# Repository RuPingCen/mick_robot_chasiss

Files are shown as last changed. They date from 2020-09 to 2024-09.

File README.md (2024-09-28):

# mick_robot_chasiss

项目文档：https://mickrobot.github.io/ 

本项目描述了针对室外环境设计的一个开源ROS小车底盘，项目开源了小车的3D机械图，基于STM32设计的小车控制板，电源板（为传感器供电）；小车的**PCB**、**代码**及**3D图纸**均是开源，大家可以自行下载打样学习。

- **master分支 为第3版小车 MickX4-V3（ 最新版）**，
- MickX4-V2分支为第2版小车代码分支。 
- M4分支为麦克纳姆轮第一版小车代码分支。[项目更新日志](https://github.com/RuPingCen/mick_robot_chasiss/tree/master/更新日志.md)

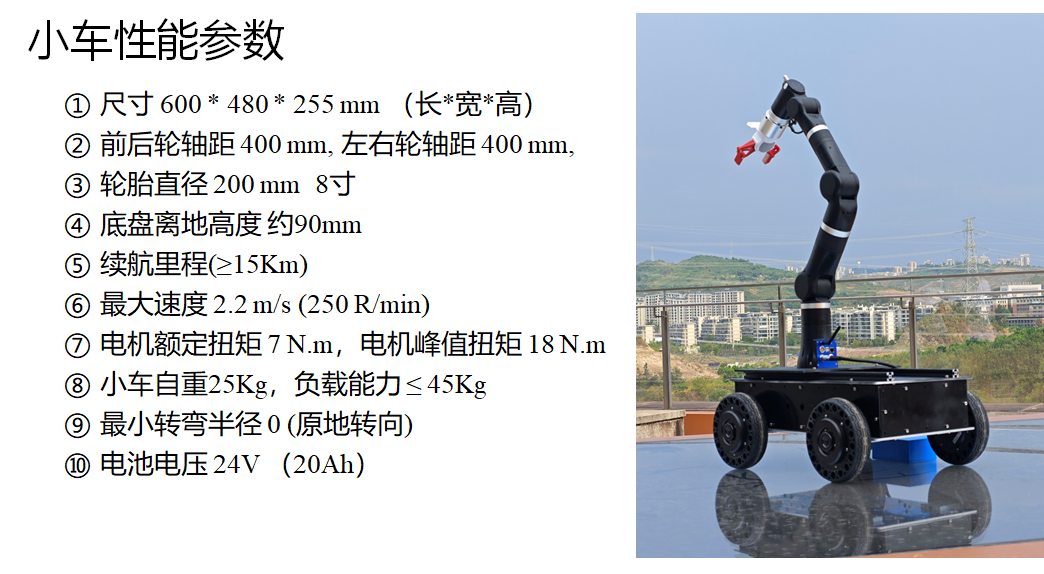
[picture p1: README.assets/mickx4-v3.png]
mickx4-v3-1




**文件目录说明**

- **ROS_Node**：小车底盘配套的ROS节点，其功能为对外发布小车里程计数据，接收ros cmd_vel话题控制命令控制小车移动

- **STM32_Code**：存放小车上嵌入式控制板的代码文件，控制器采用STM32F407

- **3D_Model_xxx**：存放小车3D模型文件

- **PCB_File**：存放小车上所用PCB文件

- **Reference_Documents**：存放相关的传感器的使用手册等

------------------------------------------------------------------------------------------

注意：开源的电源板和控制板仅供大家自己打样学习用，切勿用于商业用途。问题、项目合作可联系 cenruping@vip.qq.com，可以代为调试、新开发线控底盘或针对已有的小车底盘设计**工业版控制器**及**大功率电源模块**。也欢迎加QQ群讨论交流  1149897304 (开源ROS自主导航小车)；

- 小功率电源板-[淘宝链接](https://item.taobao.com/item.htm?spm=2013.1.w4023-18698948782.10.3cd752e6AWcwLT&id=702856225631)
- 大功率电源模块-[淘宝链接](https://item.taobao.com/item.htm?spm=a213gs.success.result.1.5ac34831gMQFX4&id=746778756080)
- 控制板-V1-[淘宝链接](https://item.taobao.com/item.htm?spm=2013.1.w4023-18698948782.7.5ec21803wgmf68&id=649231129557)

------------------------------------------------------------------------------------------

## 1 启动差速小车底盘
master分支代码文件可适配**两轮**、**四轮差速小车**。两轮差速底盘，需要把底盘电机ID设置为1和3即可使用4轮差速底盘相同的命令。

###  1.1 连线配置小车

==注：==[小车的搭建、连线，遥控器操作说明](https://github.com/RuPingCen/mick_robot_chasiss/tree/master/小车组装说明.md) 

### 1.2 启动小车ROS节点

ROS节点与控制板的通讯协议：  https://docs.qq.com/sheet/DV2hmSEdSYVVtclB4 

小车的配套的ROS节点位于 https://github.com/RuPingCen/mick_robot_chasiss/tree/master/ROS_Node 

该**ROS_Node**目录中包含两个文件夹： **mick_bringup**和**mick_description** ，**mick_bringup**为小车对应的ROS驱动节点，**mick_description**为urdf模型。

**step1:** 将ROS_Node中的mick_bringup目标代码拷贝到ROS工作空间进行编译

```shell
cp -r mick_bringup ~/catkin_ws/src
cd ~/catkin_ws/src
catkin_make
```

**step2**： 通过USB转232串口线连接电脑和小车控制板，

修改串口权限（可以查看设备的ID号 ls /dev/ttyUSB*）

```
sudo chmod 766 /dev/ttyUSB0
```

 或者根据串口设备的标识符去设置串口别名

```
cd mick_bringup/scripts
sudo cp ultrasonic.rules /etc/udev/rules.d/
```

把文件拷贝到/etc/udev/rules.d目录下就可以使用 /dev/mick替代 /dev/ttyUSB0 来访问模块了

**step3:** 启动ROS节点

```shell
roslaunch mick_bringup mickrobot_v3.launch
```

小车节点启动以后可以通过rostopic list命令查看到该ROS节点会对外发布如下Topic

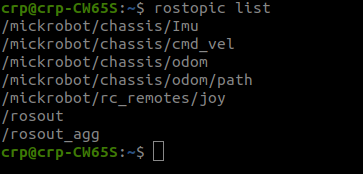
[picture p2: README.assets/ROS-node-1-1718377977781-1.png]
ROS-node-1


其中：

- /mickrobot/chassis/Imu     对外发布小车自身IMU测量数据
- /mickrobot/chassis/odom  小车里程计数据
- /mickrobot/chassis/odom/path   小车里程计数据对应的路径（默认不发布）
- /mickrobot/rc_remotes/joy  遥控器数据（默认不发布）
- /mickrobot/chassis/cmd_vel    小车控制命令接收话题

mickrobot_v3 launch文件内容如下：

```xml
<launch>
  <node pkg="mick_bringup" type="mickx4_bringup_v3" name="mickrobot" output="screen">

	  <param name="dev" value="/dev/ttyUSB0" type="str" />
	  <param name="baud" value="115200" type="int" />
	  <param name="time_out" value="1000" type="int" />
	  <param name="hz" value="100" type="int" />

	  <param name="chassis_type" value="0" type="int" /> <!--0: 差速底盘  1: 麦克纳姆轮底盘 2:阿卡曼转向  3全向-->

	  <param name="sub_cmdvel_topic" value="chassis/cmd_vel" type="str" />
	  <param name="pub_odom_topic" value="chassis/odom" type="str" />
	  <param name="pub_imu_topic" value="chassis/Imu" type="str" />
	  
	  <param name="is_pub_path" value="1" type="int" /> <!--0: 不发布底盘轨迹  1: 发布 -->
	</node>
</launch>
```

**step4**: 新建终端，通过ROS话题向  **/mickrobot/chassis/cmd_vel** 话题发布数据 控制小车移动（**注意 将遥控器左上角拨码开关拨到最上，表示开启自动驾驶模式**）

```shell
rostopic pub /mickrobot/chassis/cmd_vel -r 10 geometry_msgs/Twist "linear:
  x: 0.0
  y: 0.0
  z: 0.0
angular:
  x: 0.0
  y: 0.0
  z: -0.1" 
```

角速度方向： 逆时针为正，速度方向：车头方向为x方向。

**step5**:  或通过键盘遥控小车底盘（step4和step5选其中一个即可）

这里借助turtlebot3提供的键盘控制节点，检验小车与ROS节点通讯是否正常

注意：需要安装  **sudo apt-get install ros-noetic-turtlebot3-teleop** 包

```shell
export TURTLEBOT3_MODEL=burger
roslaunch turtlebot3_bringup turtlebot3_model.launch
```

## 2 小车控制板

## 2.1 小车控制板V3

第3版小车控制板采用了STM32F407作为主控制器

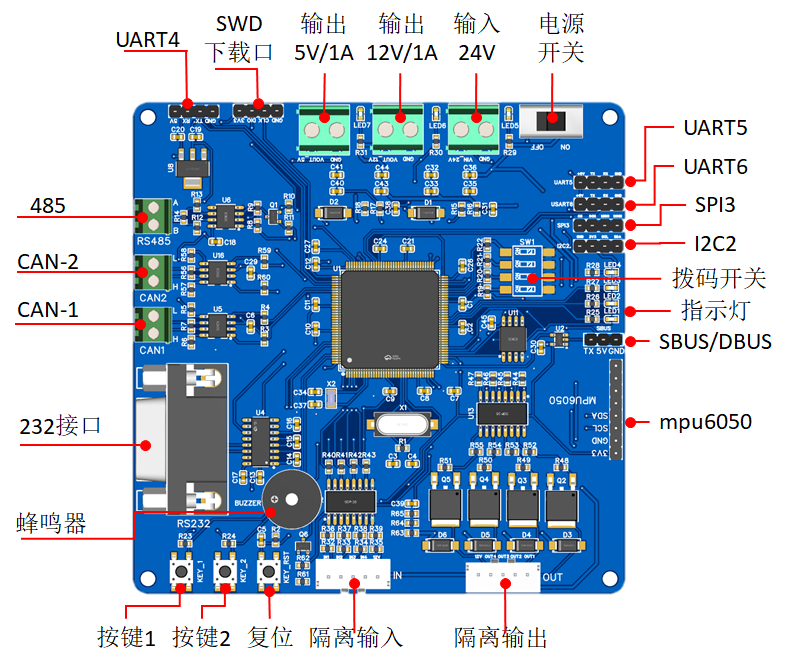
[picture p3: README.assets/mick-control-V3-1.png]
mick-control-V3-1


### 2.2 小车控制板V1

第一版控制板采用STM32F103作为主控制芯片。控制板输入20-36V DC直流，对外提供1路DC 5V 2A 、1路DC 12V 2A 对车载传感器供电。

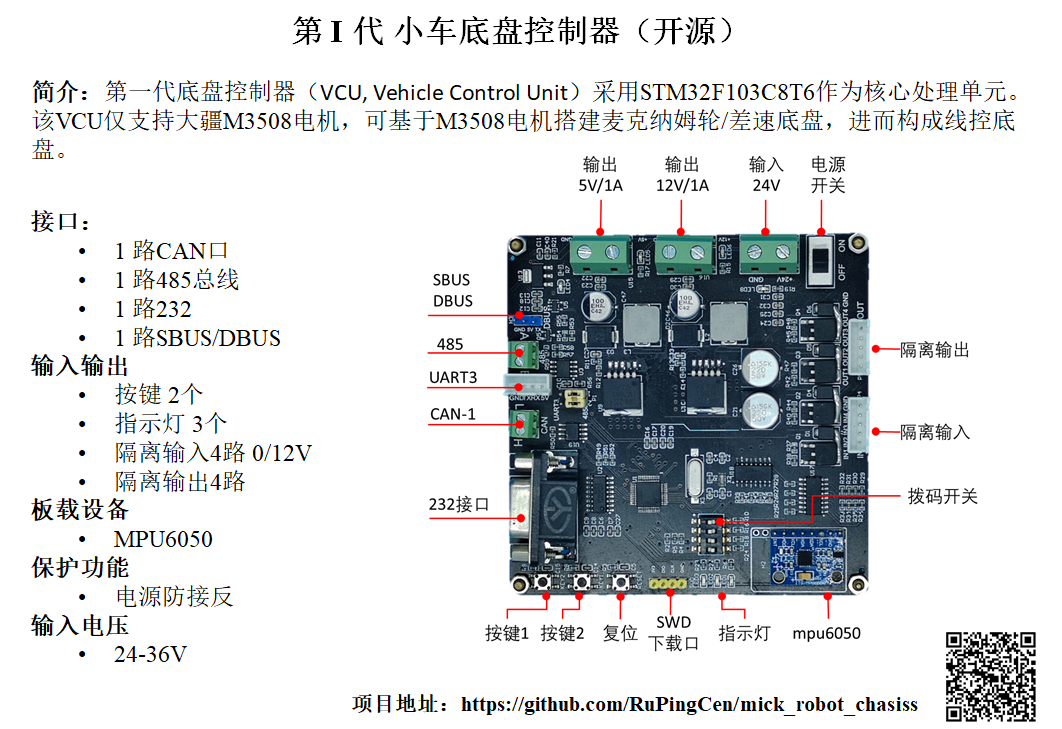
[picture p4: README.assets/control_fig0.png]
control_fig0


提供1路DBUS接口、1路232接口、1路CAN总线、1路485接口、1路UART3接口（与485复用）、1路IIC。其中DBUS被用来接收遥航模遥控器的数据，232接口负责与上位机ROS通讯。CAN总线连接4个M3508电机。IIC连接板子上安装的MPU9250。485接口和UART3接口复用，可扩展其他传感器模块。
3路LED指示灯用于显示程序状态。2路按键、4路拨码开关用于调试和选择程序功能。4路隔离输入（输入电压范围12-24V）。4路隔离输出（输出高阻态和GND，承受电流2A）。

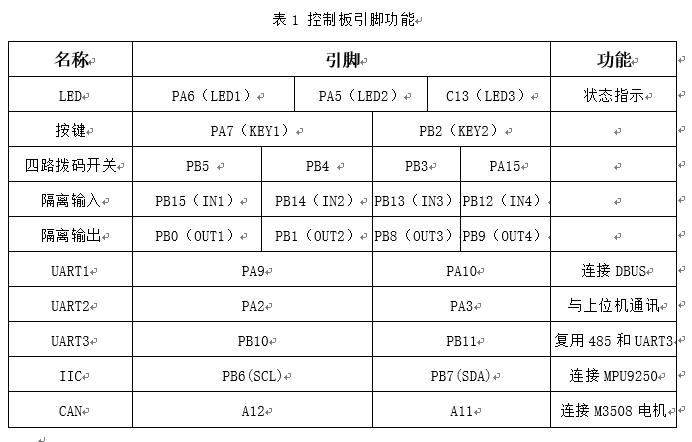
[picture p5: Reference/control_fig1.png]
control_fig1


### 2.2 小车控制板外形尺寸

第1版和第3版的小车控制板外形和安装孔位一致。

板子外形为99*99 mm 安装孔位于四周呈轴对称分布，孔中心间距为93mm,孔直径为φ3.1 mm。如下图所示。

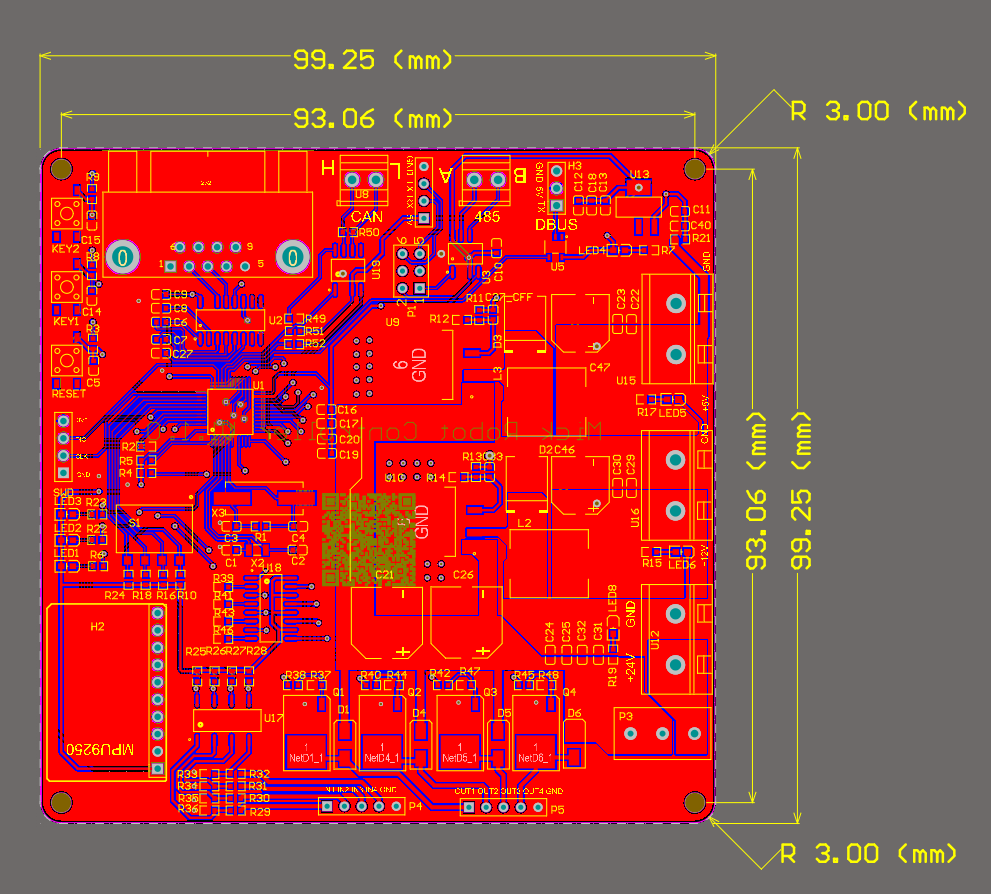
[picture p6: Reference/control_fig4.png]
control_fig4


## 3 小车电源板-功能说明
如下图所示，设计如下电源板以满足对工控机和自主导航小车车载传感器供电需求。

- 输入20-36V DC直流，
- 输出1路DC 5V 2A 
- 输出1路DC 3.3-19V 2A 可调电源 
- 输出1路DC 12V 3.5A
- 输出1路DC 19V 3.5A

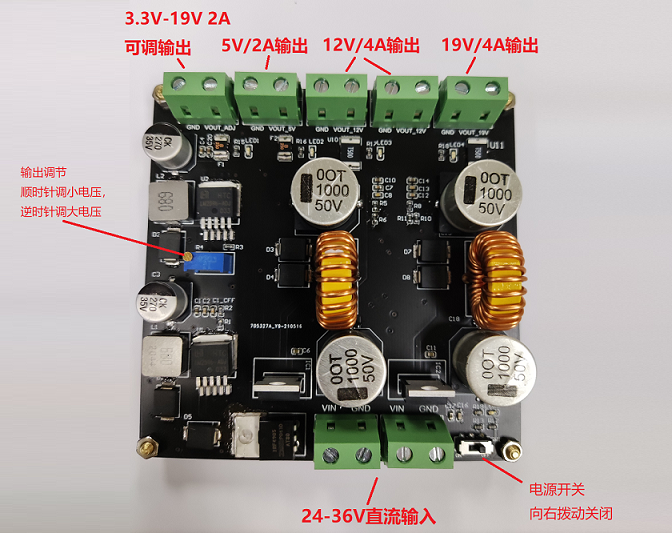
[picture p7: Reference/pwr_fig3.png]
pwr_fig1


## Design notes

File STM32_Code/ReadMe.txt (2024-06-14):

=========================================================================================
# 2024-4-30
1、增加了 里程计函数 利用IMU数据矫正 差速底盘航向角不准的问题
 =========================================================================================

=========================================================================================

1、增加了MPU6050 DMP 函数
2、增加了FLASH 数据读取函数
3、增加了Euler电机 控制数据发送函数，状态读取未完善
 =========================================================================================

限制了阿卡曼转向半径
printf改为网口输出
增加后轮阿卡曼转向模型   2023.9.25日调试 OK

轮毂电机修改：（未调试）

	0. 初始化函数 MOTOR_APSL2DB_Init 中 34-42行代码增加了其他报警指令清除  06 0f  (先松轴再上电流程)               OK

	1. 初始化函数 MOTOR_APSL2DB_Init   加入  MOTOR_APSL2DB_Infor_Get函数 读取电机信息并打印到网口    未通过测试

	2.增加每个1秒钟读取一次电机状态数据，温度，避免电机错误码通过CAN总线返回的时候不能及时读取到   175行

	3.增加调试，一旦电机有过载，就让灯变红  156-159行

	4. 限制电机电流环工作电流？   607300   写入值 1448 （15A）电流
	// 读取电流
	void MOTOR_APSL2DB_Read_CurrentLimt(uint16_t ID)
	{
		MOTOR_APSL2DB_Read_Cmd(ID,0x6073,0x00); // 电流环限制电流
	}
	// 设置电机电流环工作电流
	void MOTOR_APSL2DB_Set_CurrentLimt(uint16_t ID, uint16_t curr_value)

	5.读取驱动器温度  APS_L2DB_Read_Temp（）；

调试0-1是否可以使电机正常初始化
调试4 是否设置参数有效

增加重启接口

####  更新日志

    - 增加DBUS解析模块，串口2以 DMA模式 接收固定长度数据

2023-4-26
    - 增加以太网模块、DBUS、虚拟示波器函数（PID调试）
	
2023-4-25
    -  添加串口DMA传输

2023-2-3

	- 添加GPIO输入输出封装函数、外部触发中断接口函数、串口1-串口6初始化、发送、接收中断接口函数、定时器中断函数
 
## 目录说明

	Bsp 目录存放在底层硬件库基础上封装的二次接口

	Usr 主函数及外设相关函数文件

	Libraries STM32F4官方库文件

	Output 编译输出文件

	Listing 编译工程时产生的中间文件

	Project 存放keil工程文件
	
	Doc  存放测试文件以及参考文献、资料
	
##  备注

* 晶振问题：系统默认使用时钟为25Mhz  若使用8Mhz的晶振则需要   https://blog.csdn.net/qq1291917670/article/details/111356293
*   1、把 system_stm32f4xx.c 的 #define PLL_M 25 中的 25改为8
*   2、 把stm32f4xx.h中 #define  HSE_VALUE 	((uint32_t)25000000)   中的 25000000改为8000000

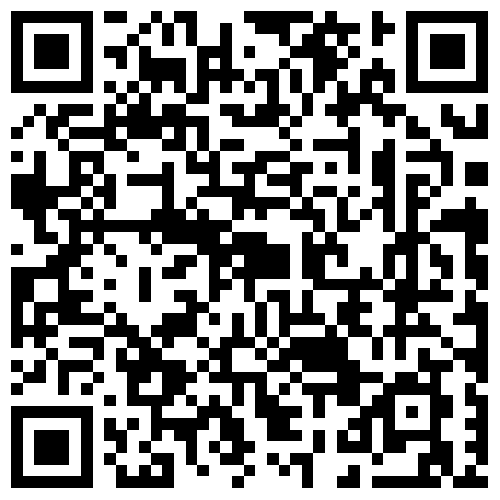
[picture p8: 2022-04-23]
开源项目地址.png

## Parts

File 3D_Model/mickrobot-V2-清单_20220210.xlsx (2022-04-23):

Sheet: 底盘器件清单
机加工类
序号 | 名称 | 规格 | 图片 | 数量 | 单价 | 小计 | 参考链接
1 | 铝型材 | 60mm |  | 12 | 332 | 332
 |  | 300mm |  | 4
 |  | 320mm |  | 12
 |  | 360mm |  | 4
 |  | 438mm |  | 4
 |  | 500mm |  | 8
 |  | 572mm |  | 4
2 | L型型材 | 360mm打孔 |  | 4 | 21 | 84 | 注：型材和L型型材在同一家店加工，共计428.6元，含税包邮
3 | 电机轴 | 直径16mm，长128mm |  | 9 | 62.3 | 560
4 | 轮胎连接法兰 | 直径60mm，长41mm |  | 9 | 102.3 | 920 | 注：电机轴和法兰在同一家店加工，共计1480元，含税包邮
5 | 3mm铝合金板 | 612*420mm |  | 2 | 250 | 500
 |  | 612*360mm |  | 2
6 | 3D打印同步轮张紧器 | 定制 |  | 5 | 110 | 550 | 注：备用件1个
合计 |  |  |  |  |  | 2946
机械购买类
序号 | 名称 | 规格 | 图片 | 数量 | 单价 | 小计 | 参考链接
1 | 内六角螺栓 | M4x10 |  | 50 | 0.11 | 5.52 | https://detail.tmall.com/item.htm?spm=a1z0d.6639537.1997196601.14.b6c97484Jxu5DM&id=623654092434
 |  | M5x10 |  | 100 | 0.153 | 15.3
 |  | M5x12 |  | 140 | 0.17 | 23.8
 |  | M5x16 |  | 60 | 0.204 | 12.24
 |  | M5x25 |  | 60 | 0.272 | 16.32
2 | T型螺母 | M5 |  | 210 | 0.15 | 31.5 | https://detail.tmall.com/item.htm?spm=a1z0d.6639537.1997196601.68.b6c97484Jxu5DM&id=659525116182
3 | 防松垫片 | M5 |  | 200 | 0.045 | 9 | https://detail.tmall.com/item.htm?spm=a1z0d.6639537.1997196601.104.b6c97484Jxu5DM&id=591388288527
4 | 平垫片 | M5x110x1 |  | 200 | 0.05 | 10 | https://detail.tmall.com/item.htm?spm=a1z0d.6639537.1997196601.95.b6c97484Jxu5DM&id=587264448921
5 | 尼龙垫片 | M6x14x1 |  | 200 | 0.06 | 12 | https://detail.tmall.com/item.htm?spm=a1z0d.6639537.1997196601.113.b6c97484Jxu5DM&id=591802201517
6 | 防松螺母 | M5 |  | 210 | 0.126 | 26.46 | https://detail.tmall.com/item.htm?spm=a1z0d.6639537.1997196601.86.b6c97484Jxu5DM&id=586273553071
7 | 直径16mm轴用挡圈 | 16mm |  | 50 | 0.16 | 8 | https://detail.tmall.com/item.htm?spm=a1z0d.6639537.1997196601.77.b6c97484Jxu5DM&id=622476185093
8 | 大同步轮 | 5m-40齿-10带宽-16内孔 |  | 9 | 38 | 342 | https://detail.tmall.com/item.htm?id=525872457550&from=detail&spm=a212db.24065199
9 | 小惰轮 | 3m-25齿-光面 |  | 9 | 13 | 117 | https://item.taobao.com/item.htm?spm=a1z0d.6639537.1997196601.403.b6c97484Jxu5DM&id=536551192197
10 | 同步带 | 5m-1250-10带宽 |  | 5 | 14.8 | 74 | https://detail.tmall.com/item.htm?id=16317594110&sku_properties=122216904:20213
11 | 平键 | M5x5x40 |  | 10 | 1.25 | 12.5 | https://detail.tmall.com/item.htm?spm=a1z0d.6639537.1997196601.68.b6c97484wzS99l&id=638386905688
 |  | M4x4x10 |  | 20 | 0.29 | 5.8
12 | 铝型材连接角码 | 2020 |  | 100 | 0.8 | 80 | https://detail.tmall.com/item.htm?spm=a1z0d.6639537.1997196601.14.b6c97484wzS99l&id=591722140740
13 | 轴承座 | 支座 |  | 8 | 170 | 1360
14 | 橡胶轮胎 | 10英寸安装孔径10mm带键槽 |  | 8 | 155 | 1240 | https://item.taobao.com/item.htm?spm=a1z09.2.0.0.6c0a2e8d2s5F8e&id=571568874487&_u=en99pfa797d
15 | 钢柱 | M4x15，外圆8mm |  | 9 | 1.2 | 10.8 | https://item.taobao.com/item.htm?spm=a1z0d.6639537.1997196601.516.b6c97484wzS99l&id=44262120541
合计 |  |  |  |  |  | 3412.24
电气购买类
序号 | 名称 | 规格 | 图片 | 数量 | 单价 | 小计 | 参考链接
1 | 3508电机 | M3508 |  | 8 | 498 | 3984 | https://item.taobao.com/item.htm?spm=a1z10.5-c-s.w4002-22661058769.12.728f6cb7EHD1pg&id=564693598973
2 | C620驱动器 | C620 |  | 8 | 398 | 3184 | https://item.taobao.com/item.htm?spm=a1z10.5-c-s.w4002-22661058769.48.728f6cb7EHD1pg&id=564838441242
3 | 电池支架 |  |  | 4 | 198 | 792 | https://item.taobao.com/item.htm?spm=a1z10.5-c-s.w4002-22661058769.24.2ada6cb7ycxJMB&id=564512528295
4 | 电池 | TB47 |  | 4 | 1398 | 5592 | https://item.taobao.com/item.htm?spm=a1z10.5-c-s.w4002-22661058769.27.2ada6cb7ycxJMB&id=584616235012
合计 |  |  |  |  |  | 13552
总计约 |  |  |  |  |  | 19910.24

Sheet: 说明
底盘参数
1、底盘尺寸为500*400
2、前后轮的中心轮距为450，左右轮子的中心轮距为400

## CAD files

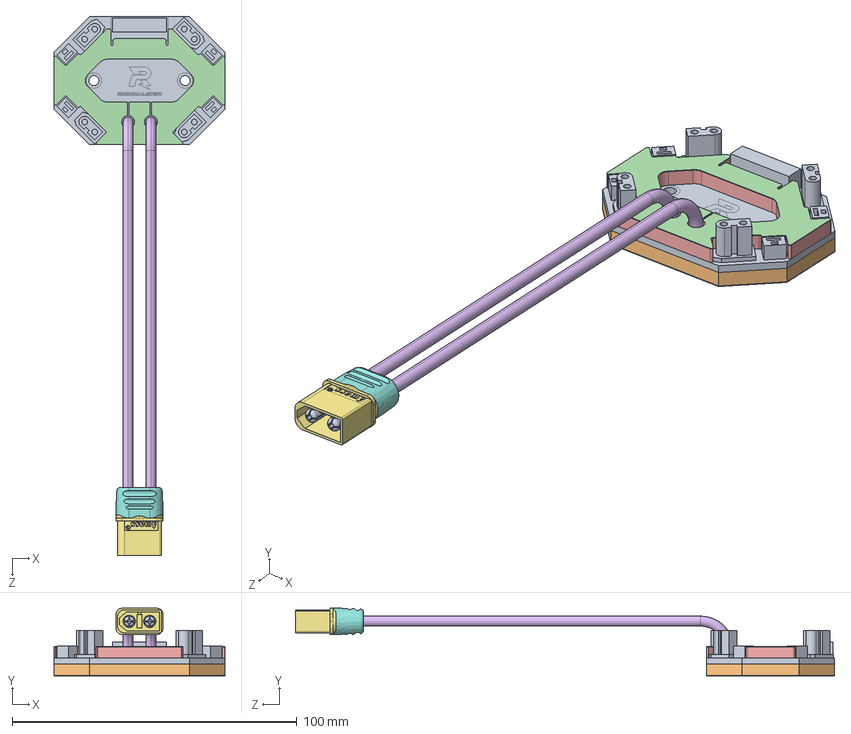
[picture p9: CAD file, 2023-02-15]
Reference_Documents/电机M3508_C620电调/M3508附件包_集线板.STEP
60.0 x 23.7 x 189.2 mm

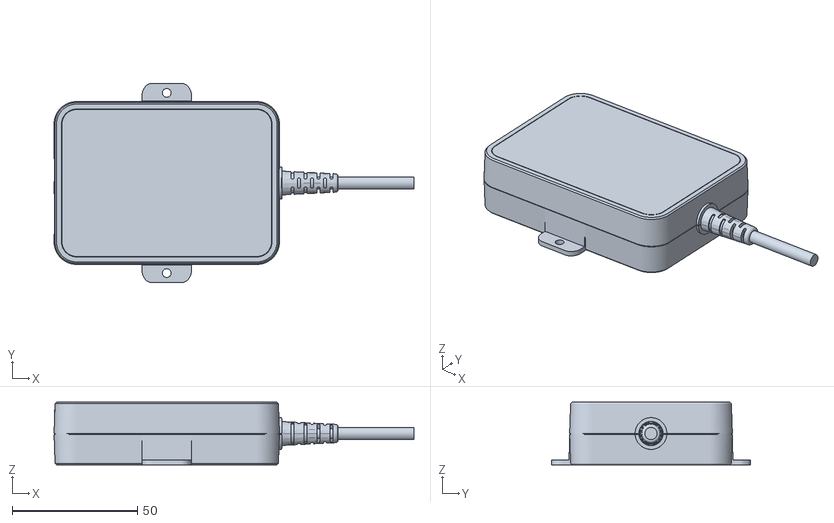
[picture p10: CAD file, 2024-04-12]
ROS_Node/mick_description/urdf/mesh/RS-LiDAR-32 Interface Box.stl
143.7 x 79.6 x 25.0

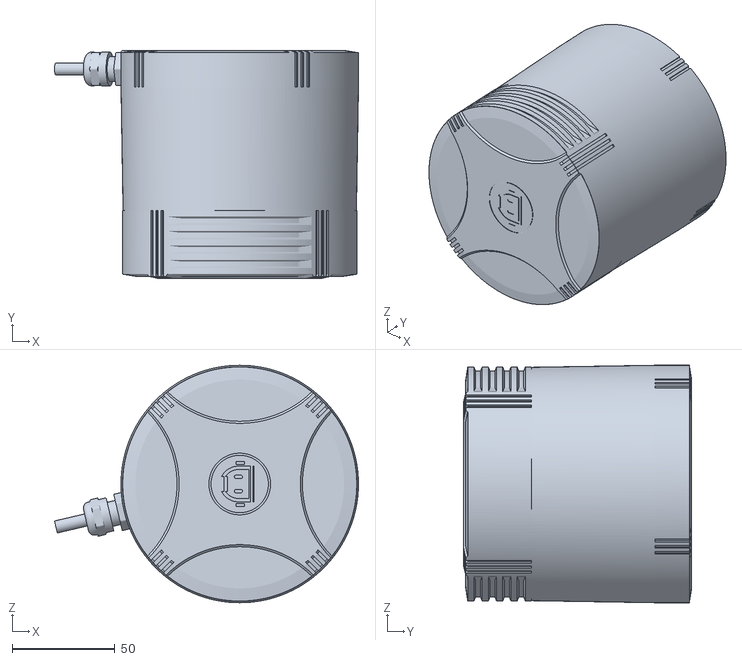
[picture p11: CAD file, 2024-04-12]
ROS_Node/mick_description/urdf/mesh/RS-LiDAR-32.stl
147.8 x 110.7 x 115.5

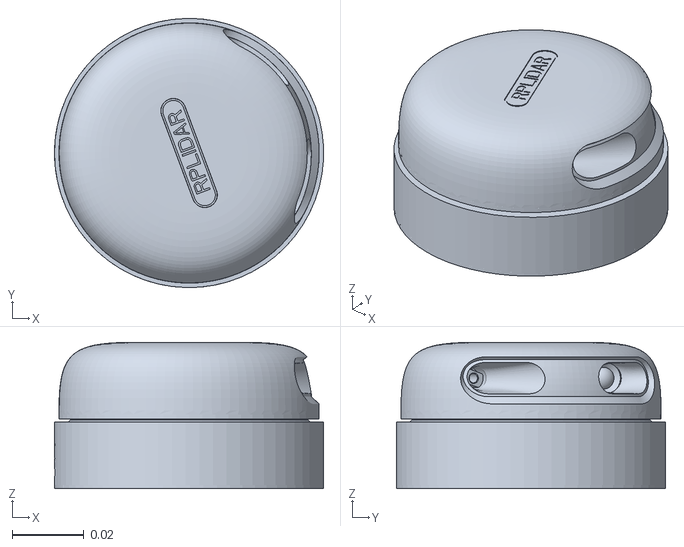
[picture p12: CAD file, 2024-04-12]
ROS_Node/mick_description/urdf/mesh/rplidar_a2.stl
0.075 x 0.075 x 0.0408

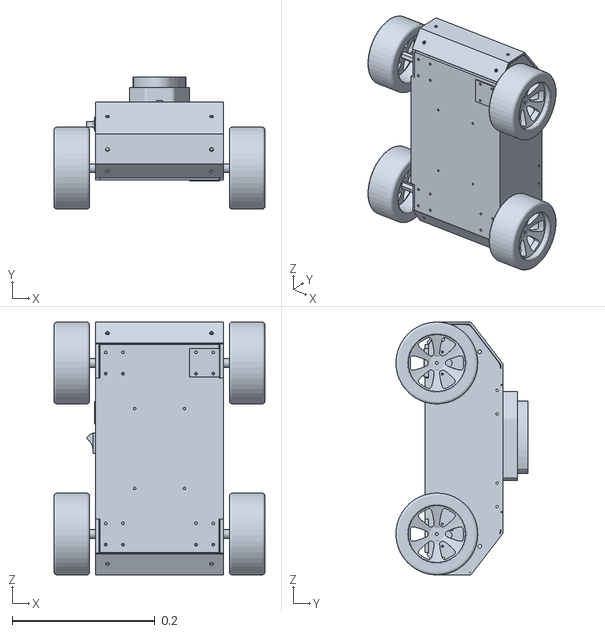
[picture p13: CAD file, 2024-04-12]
ROS_Node/mick_description/urdf/mesh/autolabor.stl
0.296 x 0.185 x 0.355

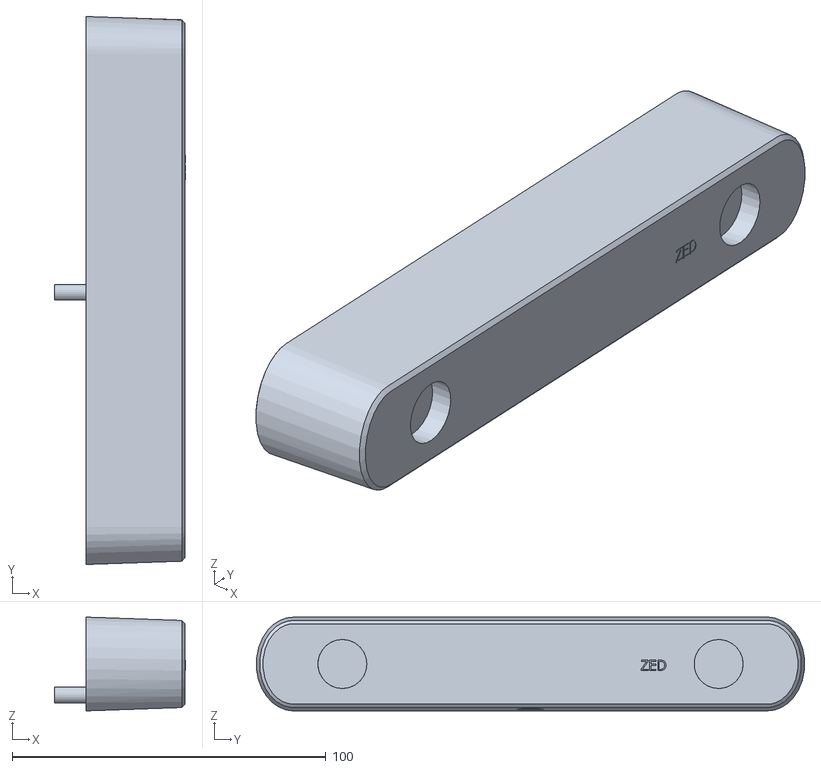
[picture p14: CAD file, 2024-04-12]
ROS_Node/mick_description/urdf/mesh/ZED.stl
41.8 x 174.8 x 29.9

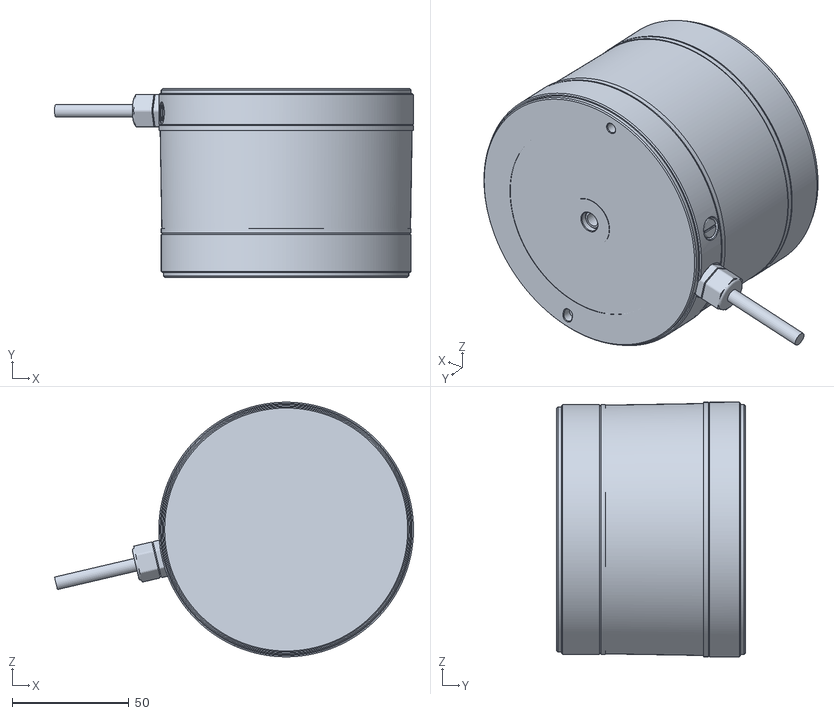
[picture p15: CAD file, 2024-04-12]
ROS_Node/mick_description/urdf/mesh/RS-LiDAR-16.stl
153.7 x 80.7 x 109.0

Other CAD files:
ROS_Node/mick_description/urdf/mesh/ZED2.stl

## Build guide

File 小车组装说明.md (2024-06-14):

#  小车平台

该小车是一款简易的4轮差速小车，通过4个轮毂电机实现小车差速运动，该小车是mick差速小车的第3版小车，该版本小车简化的小车的机械结构，选用了功率更大的轮毂电机提供动力。

## Mick-V3小车性能指标

| 名称 | 指标 |
| :---: | :---: |
| 尺寸 |  600 * 450 * 200  mm  |
|  左右轮轴距  | 400 mm |
|  前后轮轴距  | 400 mm |
| 轮胎直径 | 170 mm |
| 最小转弯半径 | 0 |
| 小车最大速度 | 2.2 m/s (250 R/min) |
| 电机额定扭矩 | 7 N.m |
| 电机峰值扭矩 | 18 N.m |
| 负载能力 | ≤40Kg |
| 续航里程 | ≥15KM |

## 小车组装

### 电机安装
通常情况小车都是安装好以后发货，在进行维修和更换配件以后可能会对小车进行拆装。这里将小车的组装过程进行说明。

小车分上底板、下底板、电机轴卡座\*4、行进电机\*4

如下图所示，将轮毂电机固定支架安装到电机上以后，对齐之间与底板上的6个安装孔，利用配件中的 **M6-16螺丝**固定。按照此方式依次组装好4个电机。

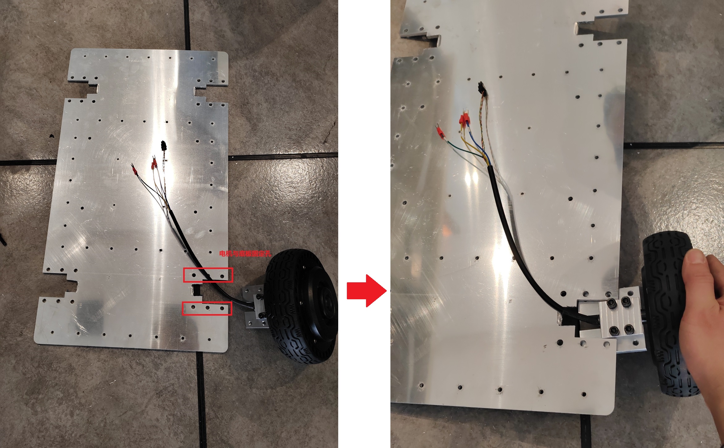
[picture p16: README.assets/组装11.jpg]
组装11


**电机驱动器**固定于下图所示两侧安装孔位置（使用**M4螺丝**）

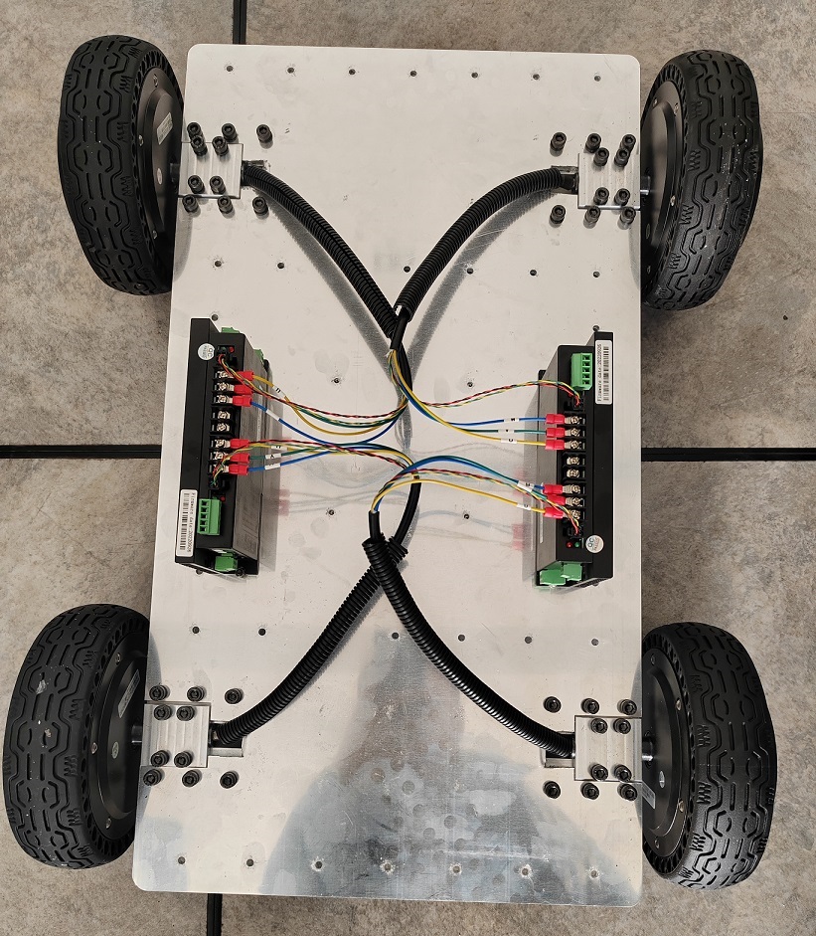
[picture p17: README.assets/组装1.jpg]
组装1


其中，驱动器散热面朝向外侧，有标注信息的一面朝向内侧。电机上U、V、W接线柱分别与电机线上标号 U（黄）、V（绿）、W（蓝）对应标号相连。

1. 左上角电机连接左侧驱动器1号位置
2. 左下角电机连接左侧驱动器2号位置
3. 右下角电机连接右侧驱动器1号位置
4. 右上角电机连接右侧驱动器2号位置

将底盘控制板通过M3铜柱安装于底盘正中间固定孔上。 

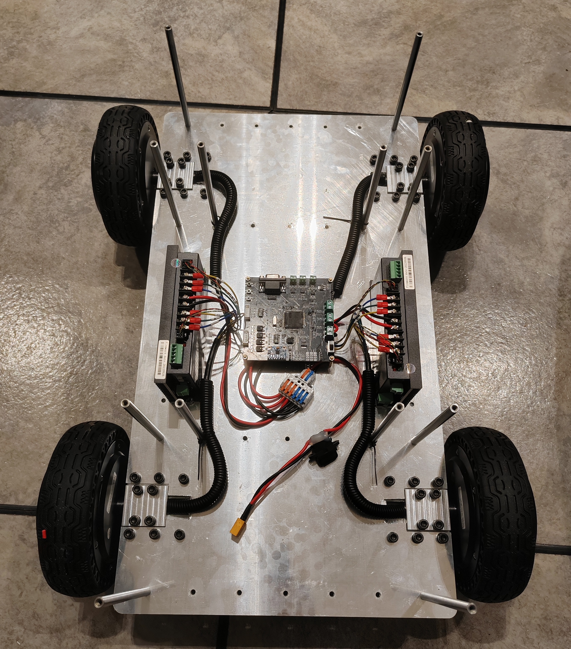
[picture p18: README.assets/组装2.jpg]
组装2


图中支撑杆（8\*100\*M4）的位置可以按上图所示进行固定，或者也可选取其他孔位固定（固定螺丝为M4）。

### 驱动器设置

step1:将小车**车头方向向前**，将左侧电机驱动器

	**SW2拨码开关BIT2（第2位开关）拨到On处**(起用CAN总线波特率1M),;

	**SW3拨码1号位置开关全部拨到oN状态**；

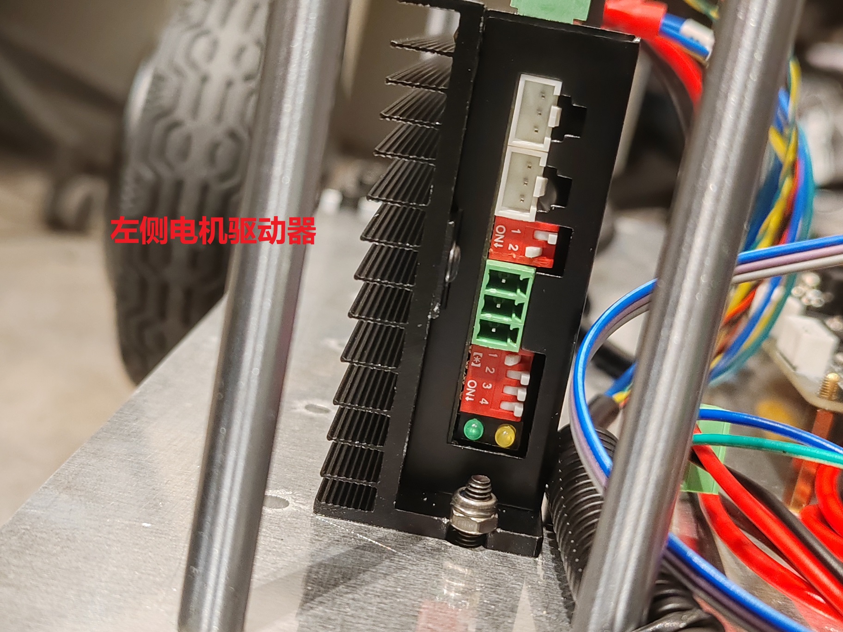
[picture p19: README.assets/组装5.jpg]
组装5


step2:将小车车头方向向前，将右侧电机驱动器

**SW2拨码开关BIT2（第2位开关）拨到On处**(起用CAN总线波特率1M),;

**==SW3拨码1号和2号位置开关全部拨到oN状态==**；

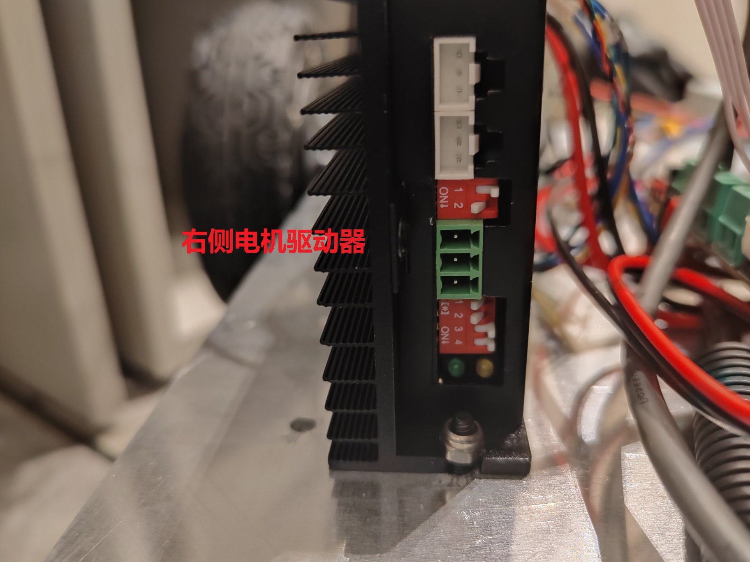
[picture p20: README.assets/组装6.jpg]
组装6


step3：将左右两侧驱动器的CAN驱动接口连接起来，并与控制板的CAN1口连接。保证控制板与两个驱动器之间形成串联结构。

## 小车控制板连线

### 与驱动器连线

控制板与电机驱动器通过CAN总线连接，连接时使用控制板CAN1通道，控制板，电机驱动器1和电机驱动器2形成串联形式。

### 与遥控器接收机连线

T8FB遥控器可以适配（R8FM和R8EF两种接收机）

接收机三个引脚（VCC、GND、Tx） 分布对应控制板（VCC、GND、Tx）引脚

接收机

##  乐迪T8FB遥控器操控说明

四轮差速小车的控制与mick开源项目中其他小车的操做方法一致。默认采用乐迪T8FB遥控器（SBUS协议）

### 遥控器配置方法

==购买整车时遥控器默认已经配置好，不需要再重新配置。==

当我们自行组装车辆或者更好遥控器时候，可以利用安卓充电线（micro usb）将遥控器与电脑连接，使用（"Reference\RadioLink_T8FB\T8S-T8FB电脑调参APP V4.2\T8S&T8FB电脑调参APP V4.2"）遥控器自带的APP进行配置。

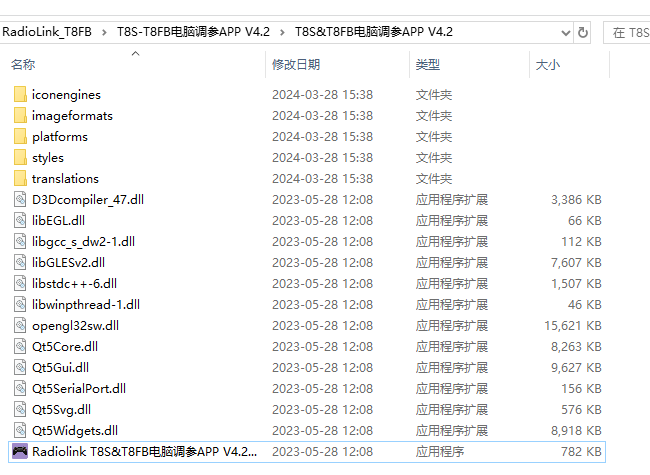
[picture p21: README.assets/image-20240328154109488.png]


在拿到遥控器的时候要注意将第1通道（右手摇杆竖直方向通道）反向，保证摇杆拉到最下方的时候遥控器输出最小值，最上方输出最大值。同时，对于水平方向通道而言，拉到最左边输出最小值，最右方向输出最大值。（可以使用乐迪官方的参数配置软件进行配置“T8S-T8FB电脑调参APP V4.2”，下图是我修改后的状态。）

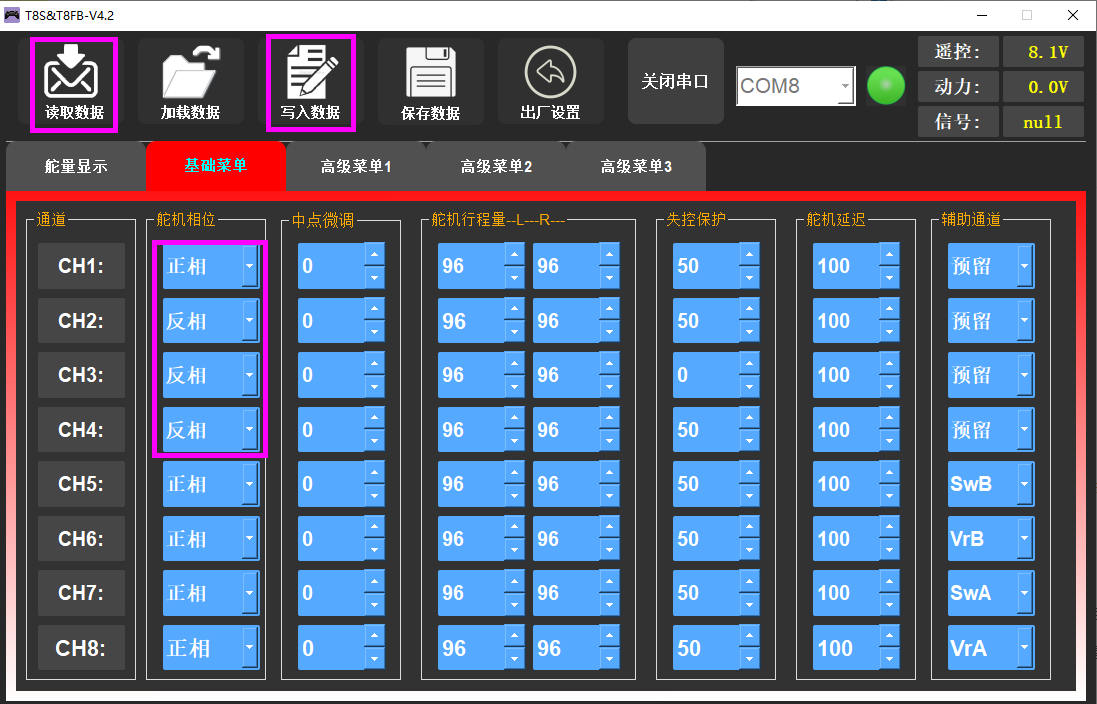
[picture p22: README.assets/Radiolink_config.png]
Radiolink_config


### 遥控器操作说明

将控制板第3号位置上的拨码开关拨到==数字侧==，表示SBUS功能。这里我用的时左手油门的RadioLink T8FB遥控器。

1. 遥控器左上角的拨动开关为功能选择按键：置于L档，即最上方位置，表示开启自动驾驶（遥控器操作无效），置于H档表示由遥控器控制小车，忽略上位机命令。
2. 遥控器右上角拨动开关上中下位置分别对应小车1m/s、2m/s、2.2m/s速度。
3. 右手边摇杆竖直方向通道控制小车前后运动（如下图所示），右边的摇杆水平通道控制小车左右旋转。

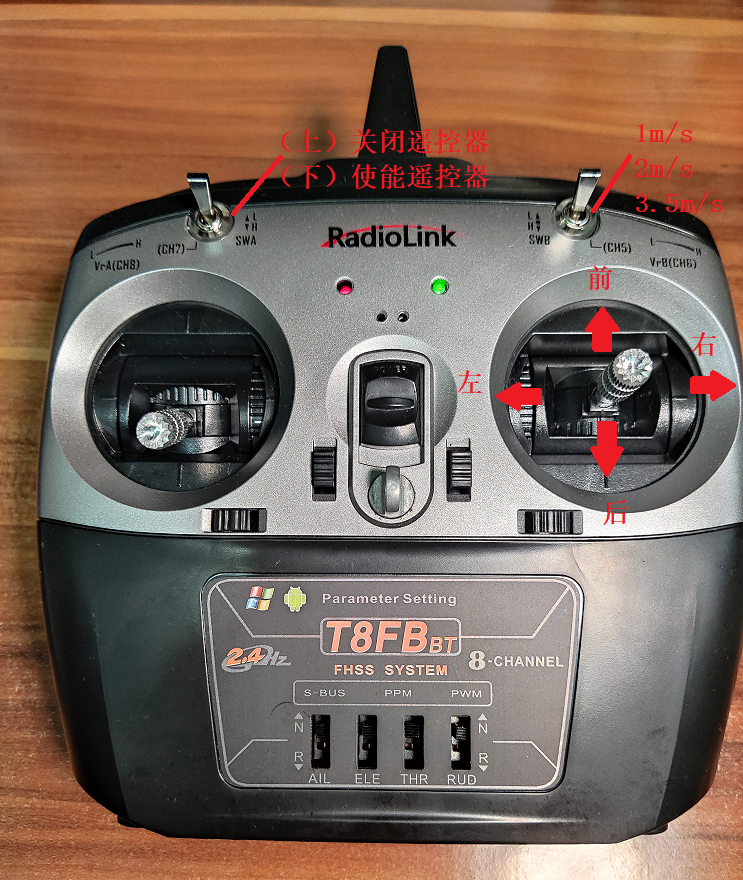
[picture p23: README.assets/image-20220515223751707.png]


### 遥控器充电

遥控器电池电压低的时候，会发出 “滴滴~”的声响，此时打开后盖将电池取出。==（注意电池插头的正负方向，对应遥控器背后”+“，”—“标识）==

遥控1

使用配套充电器充电，电池充满以后充电器的灯由红色变为绿色。遥控器充电时需使用遥控器对应的充电器，遥控器电池为2s电池，电池电压范围（6.4V-8.4V）。

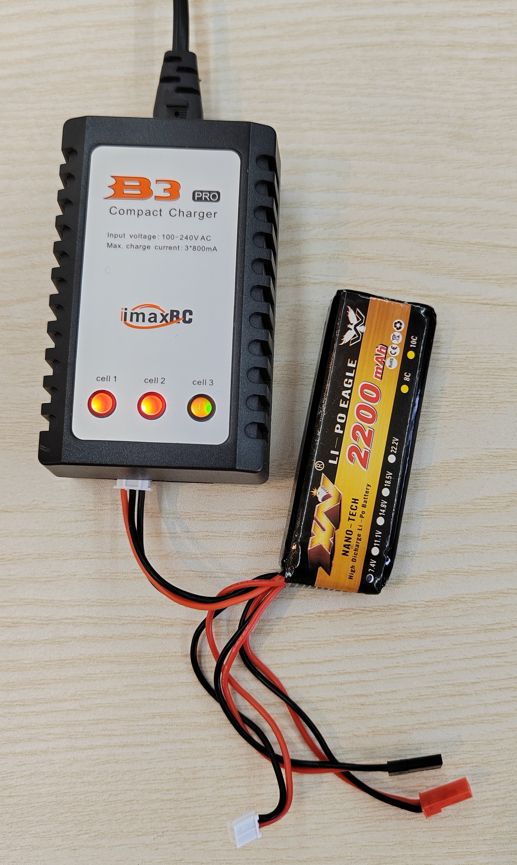
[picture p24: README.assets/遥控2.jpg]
遥控2


# 小车接口说明

## 2.1 ROS接口

小车的配套的ROS节点位于 https://github.com/RuPingCen/mick_robot_chasiss/tree/master/ROS_Node 

该**ROS_Node**目录中包含两个文件夹： **mick_bringup**和**mick_description** ，**mick_bringup**为小车对应的ROS驱动节点，**mick_description**为urdf模型。

**step1**:   将**ROS_Node**放置于ROS工作空间下进行编译

```shell
cp  -r  ROS_Node ~/catkin_ws/src  #拷贝文件到ROS工作空间
cd ~/catkin_ws/src
catkin_make
```

**step2**:   将小车USB串口连接到电脑，并赋予串口权限

```
sudo chmod 777 /dev/ttyUSB*
```

**step3**： 启动ROS节点

```
 roslaunch mick_bringup mickrobot-v3.launch
```

小车节点启动以后可以通过rostopic list命令查看到该ROS节点会对外发布如下Topic

ROS-node-1

其中：

- /mickrobot/chassis/Imu     对外发布小车自身IMU测量数据
- /mickrobot/chassis/odom  小车里程计数据
- /mickrobot/chassis/odom/path   小车里程计数据对应的路径（默认不发布）
- /mickrobot/rc_remotes/joy  遥控器数据（默认不发布）
- /mickrobot/chassis/cmd_vel    小车控制命令接收话题

**step4**: 新建终端，通过ROS话题向  **/mickrobot/chassis/cmd_vel** 话题发布数据 控制小车移动（**注意 将遥控器左上角拨码开关拨到最上，表示开启自动驾驶模式**）

```shell
rostopic pub /mickrobot/chassis/cmd_vel -r 10 geometry_msgs/Twist "linear:
  x: 0.0
  y: 0.0
  z: 0.0
angular:
  x: 0.0
  y: 0.0
  z: -0.1" 
```

角速度方向： 逆时针为正，速度方向：车头方向为x方向。

## 小车底盘与ROS节点通讯协议

### 下发接口

### 数据上传协议

# 定位建图算法

autoware环境安装

基于autoware地图构建

基于autoware地图定位

基于autoware自主导航

4G远程驾驶

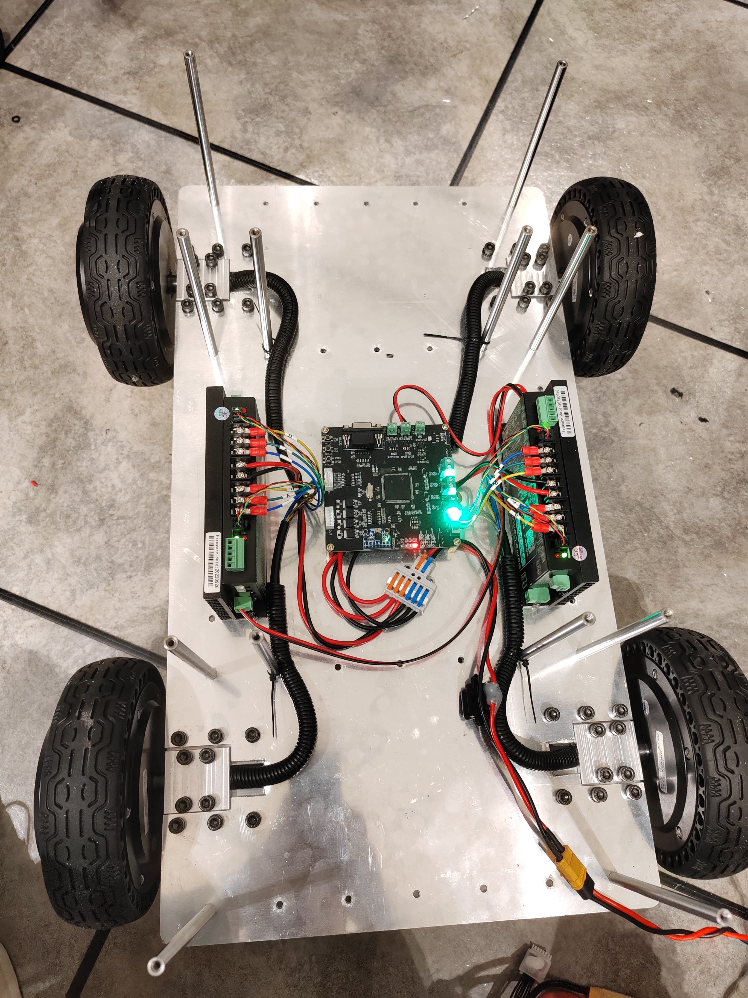
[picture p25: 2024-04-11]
README.assets/组装4.jpg

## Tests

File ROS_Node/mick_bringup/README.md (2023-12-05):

# mick_robot_bringup
该代码为麦克纳姆轮ROS底盘的ROS节点，与mick_robot_chasiss代码配合使用，更多的信息可以参考博客地址：https://blog.csdn.net/crp997576280/article/details/102026459
### V1.1 修改日志
  １．修改了ROS serial库参数，使得串口读取数据帧更加稳定

  ２．增加节点启动时候清零里程计的指令

  ３．修复了里程计掉头以后由于方向原因使得位置估算错误的BUG

  ４．增加了参数传递功能，可通过launch文件传递参数

### Ｖ1.0 修改日志
  第一次提交

# 下载安装
 1.安装依赖项

    sudo apt-get install ros-kinetic-serial

 2. cd catkin_ws/src

 3.  git clone  https://github.com/RuPingCen/mick_robot_bringup.git

 4. catkin_make

# 参数说明

sub_cmdvel_topic(接收话题名称)

pub_odom_topic（里程计发布话题名称）

dev（串口设备名称）

baud（串口波特率）

hz（里程计发布频率）

chassis_type（底盘类型选择） **0**： 表示差速底盘 **1**：表示 麦克纳姆轮底盘  **2**：4WS4WD移动底盘  **3**： 阿卡曼转向底盘

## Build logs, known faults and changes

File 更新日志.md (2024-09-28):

#  更新日志

**2024-6-21**

- 增加了USB通讯功能

- 添加外壳

**2024-3-29**

- 增加了对轮毂电机的支持，增大了小车载重能力（≤40Kg）

- 将主控芯片更换为 STM32F405XX

2023-11-05

- 增加MPU6050 DMP函数，直接读取6050 DMP处理单元输出数据四元数

2022-4-20

- 1、增加了对SBUS控制信号的解码程序，支持SBUS遥控器
- 2、对代码增加了注释

2021-4-18

- 1、开源了小车的电源板和小车控制板
- 2、将DBUS、上位机发送的命令移到中断函数中进行处理
- 3、将PID相关计算函数移到PID.c中
- 4、添加MPU9250 读取和姿态计算函数 

2020-9-8
- 1、更新了DBUS中的函数名称
- 2、更新遥控器信号丢失造成的数据乱码引起“疯转”的问题
- 3、统一4轮和2轮差速小车模型电机控制函数的单位为 m/s  和 rad/s 

 2019-10-07
- 添加ROS节点下发命令清零里程计数据功能

 2020-9-9 
- 更新MickM4 麦克纳姆轮底盘的代码

# 2、历史版本小车

##  2.1MickX4-V2分支

MickX4分支是基于M3508电机设计的底盘，控制主板采用V1.0的主板（STM32F103），注意这个版本的小车底盘负载能力有限。

更多的信息可以参考博客地址：https://blog.csdn.net/crp997576280/article/details/102026459

```
 git clone -b MickX4-V2 https://github.com/RuPingCen/mick_robot_chasiss.git
```

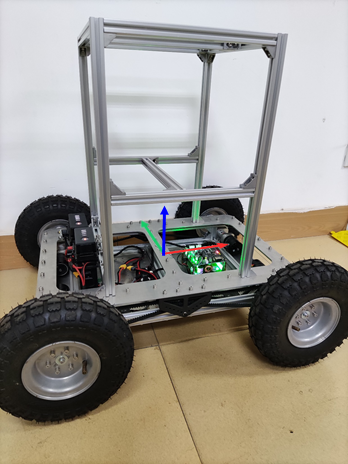
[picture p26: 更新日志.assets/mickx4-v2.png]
MickX4


## 2.2 Mick-M4 分支

MickM4分支为麦克纳姆轮ROS底盘的底盘控制程序，代码适用于STM32F103及C620电调

更多的信息可以参考博客地址：https://blog.csdn.net/crp997576280/article/details/102026459

```
 git clone -b MickM4 https://github.com/RuPingCen/mick_robot_chasiss.git
```

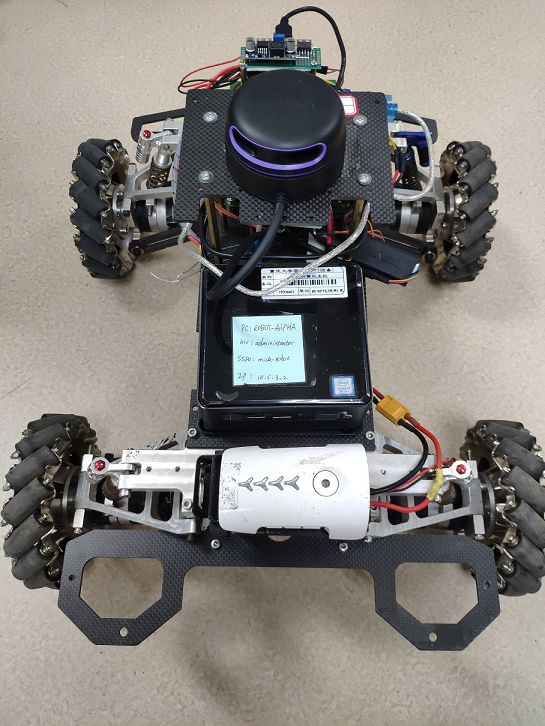
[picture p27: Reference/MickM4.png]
MickM4


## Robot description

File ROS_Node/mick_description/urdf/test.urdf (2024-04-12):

<?xml version="1.0"?>
<robot name="smartcar">
  <link name="base_link">
    <visual>
      <geometry>
        <box size="0.25 .16 .05"/>
    </geometry>
    <origin rpy="0 0 0" xyz="0 0 0.0"/>
    <material name="gree">
        <color rgba="0 0 .8 1"/>
    </material>
    </visual>
 </link>

 <link name="left_front_wheel">
    <visual>
      <geometry>
        <cylinder length=".02" radius="0.05"/>
      </geometry>
      <material name="red">
        <color rgba="1 0 0 1"/>
      </material>
    </visual>
  </link>

  <joint name="left_front_wheel_joint" type="continuous">
    <axis xyz="0 0 1"/>
    <parent link="base_link"/>
    <child link="right_front_wheel"/>
    <origin rpy="1.57075 0 0" xyz="0.12 0.1 0"/>
    <limit effort="100" velocity="100"/>
    <joint_properties damping="0.0" friction="0.0"/>
  </joint>
 <link name="right_front_wheel">
    <visual>
      <geometry>
        <cylinder length=".02" radius="0.05"/>
      </geometry>
      <material name="red">
        <color rgba="1 0 0 1"/>
      </material>
    </visual>
  </link>

  <joint name="right_front_wheel_joint" type="continuous">
    <axis xyz="0 0 1"/>
    <parent link="base_link"/>
    <child link="left_front_wheel"/>
    <origin rpy="1.57075 0 0" xyz="0.12 -0.1 0"/>
    <limit effort="100" velocity="100"/>
    <joint_properties damping="0.0" friction="0.0"/>
  </joint>
  <link name="right_back_wheel">
    <visual>
      <geometry>
        <cylinder length=".02" radius="0.05"/>
      </geometry>
      <material name="red">
        <color rgba="1 0 0 1"/>
      </material>
    </visual>
  </link>

  <joint name="right_back_wheel_joint" type="continuous">
    <axis xyz="0 0 1"/>
    <parent link="base_link"/>
    <child link="right_back_wheel"/>
    <origin rpy="1.57075 0 0" xyz="-0.12 -0.1 0"/>
    <limit effort="100" velocity="100"/>
    <joint_properties damping="0.0" friction="0.0"/>
 </joint>

  <link name="left_back_wheel">
    <visual>
      <geometry>
        <cylinder length=".02" radius="0.05"/>
      </geometry>
      <material name="red">
        <color rgba="1 0 0 1"/>
      </material>
    </visual>
  </link>

  <joint name="left_back_wheel_joint" type="continuous">
    <axis xyz="0 0 1"/>
    <parent link="base_link"/>
    <child link="left_back_wheel"/>
    <origin rpy="1.57075 0 0" xyz="-0.12 0.1 0"/>
    <limit effort="100" velocity="100"/>
    <joint_properties damping="0.0" friction="0.0"/>
  </joint>

  <link name="camera">
    <visual>
      <geometry>
        <box size=".02 .03 .03"/>
      </geometry>
      <material name="white">
          <color rgba="1 1 1 1"/>
      </material>
    </visual>
  </link>

  <joint name="camera" type="fixed">
    <parent link="base_link"/>
    <child link="camera"/>
    <origin xyz="0.1 0.0 0.025"/>
  </joint>
</robot>

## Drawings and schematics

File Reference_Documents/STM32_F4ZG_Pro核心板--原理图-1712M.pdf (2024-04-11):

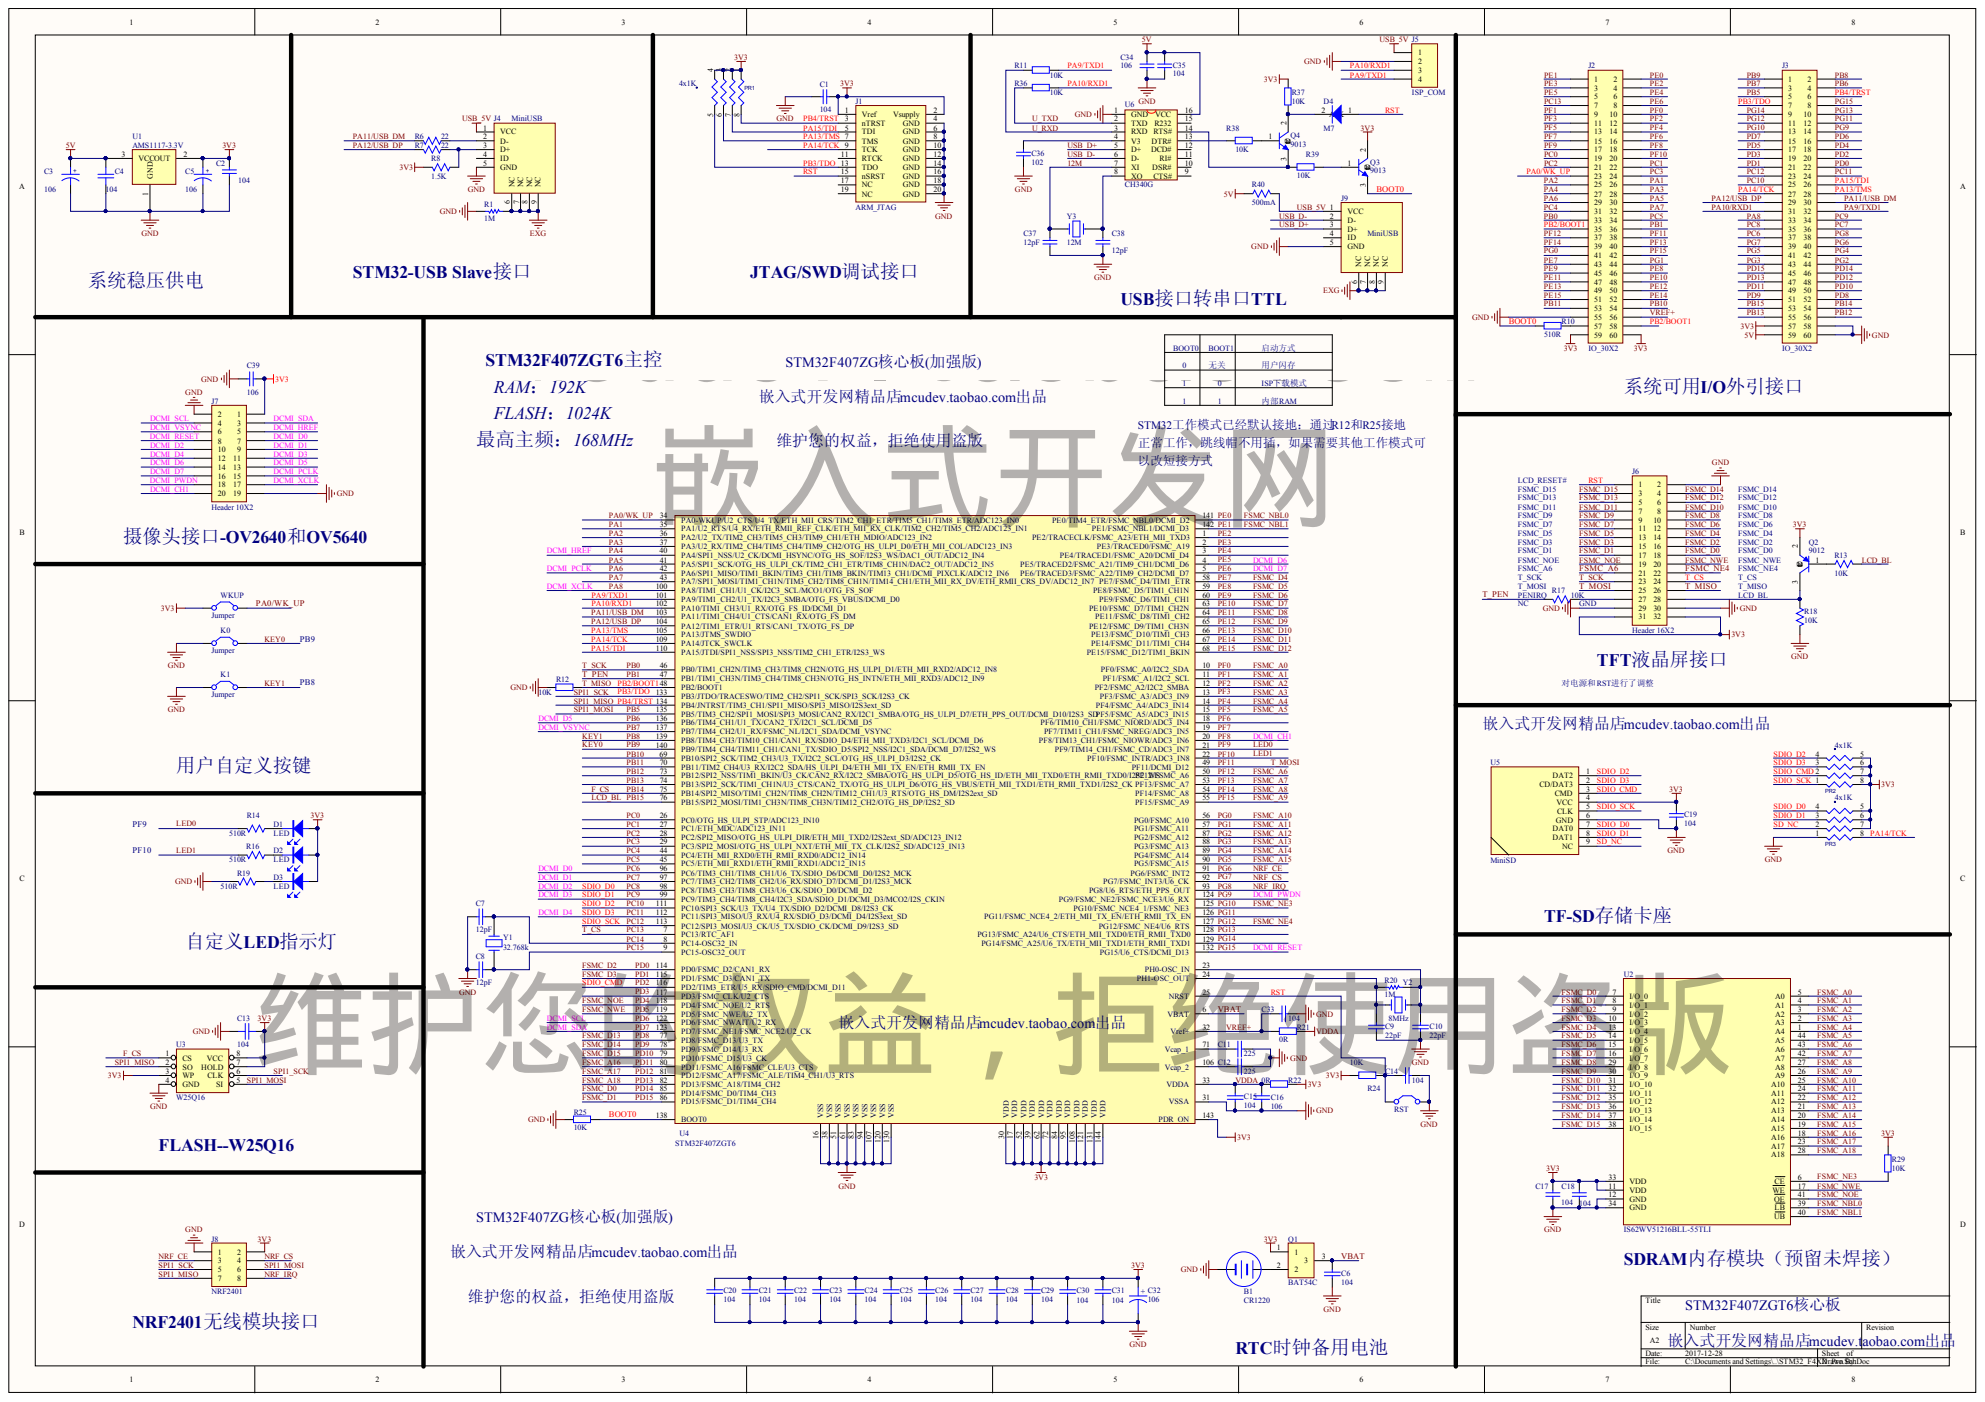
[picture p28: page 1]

0 | 无关 | 用户闪存

1 | 0 | ISP下载模式

1 | 1 | 内部RAM

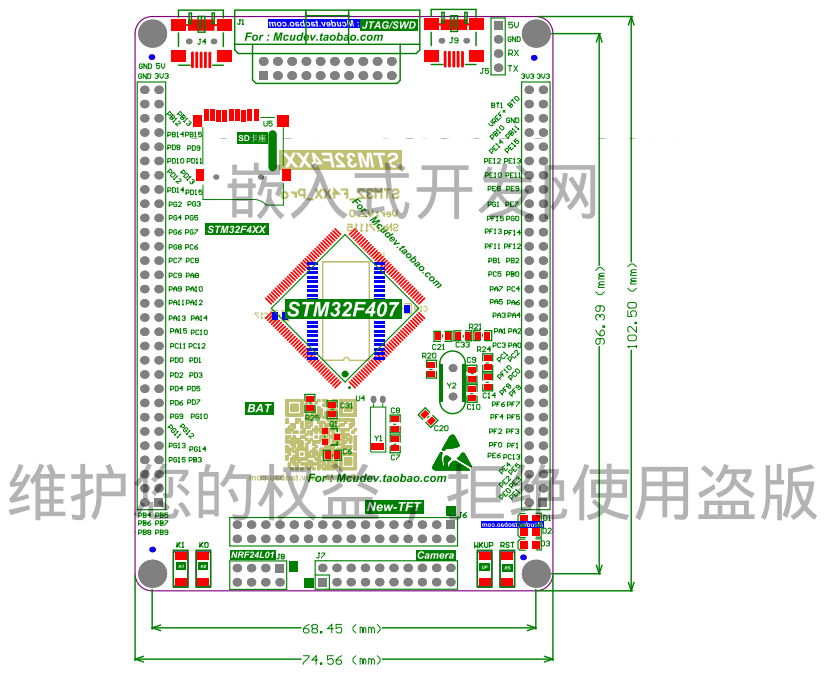
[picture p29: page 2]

Bill of Materials | <Parameter Title not found>
Source Data From: | STM32_F4XX_Pro.PrjPCB
Project: | | STM32_F4XX_Pro.PrjPCB
Variant: | | None
Creation Date: 2017-12-28 | 20:38:08
Print Date: | 43097 | 43097.85987
Footprint | Comment | LibRef | Designator | Description | Quantity
CP1220 | CR1220 | BATTERY | B1 | 1
RC0603 | 104 | Cap, Cap, CAP,
CAP, CAP, CAP,
CAP, Cap, Cap,
Cap Semi, CAP,
CAP, CAP, CAP,
CAP, CAP, CAP,
CAP, CAP, CAP,
CAP, CAP, CAP,

## Cap

C1, C2, C4, C6, C13, C14, C15, C17, C18, C19, C20, C21, C22, C23, C24, C25, C26,

## C27, C28, C29, C30, C31, C33, C35

Capacitor, Capacitor, [NoValue], Capcitor, [NoValue], Capcitor, Capcitor, Capacitor,

## Capacitor, Capacitor (Semiconductor SIM

Model), Capcitor, Capcitor, Capcitor, Capcitor, Capcitor, Capcitor, Capcitor, Capcitor, Capcitor, Capcitor, Capcitor,

## Capcitor, Ca

24

RC0805 | 106 | CAP2, CAP2, CAP, CAPACITOR POL, Cap, Cap
C3, C5, C16, C32, C34, C39 | [NoValue], [NoValue], Capcitor, Capacitor,

## Capacitor, Capacitor

6

RC0603 | 12pF | CAP | C7, C8, C37, C38 | Capcitor, Capcitor, Capacitor, Capacitor | 4
RC0603 | 22pF | CAP | C9, C10 | Capcitor | 2
RC0805 | 225 | CAP | C11, C12 | Capcitor | 2
RC0603 | 102 | Cap | C36 | Capacitor | 1
LED0805 | LED | LED | D1, D2, D3 | | 3
SOD_323 | M7 | Diode | D4 | Default Diode | 1
JTAG20P | ARM_JTAG | JTAG | J1 | JTAG | 1
IDE2X30 | IO_30X2 | Header 30X2 | J2, J3 | Header, 30-Pin, Dual row | 2
MINI_USB | MiniUSB | MiniUSB | J4, J9 | | 2
HDR1X4 | ISP_COM | Header 4 | J5 | Header, 4-Pin | 1
IDE2X16-2.54Header 16X2 | Header 16X2 | J6 | Header, 16-Pin, Dual row | 1
IDE2x10-2.54Header 10X2 | Header 10X2 | J7 | Header, 10-Pin, Dual row | 1
DIP2X4-2.54 | NRF2401 | Header 4X2 | J8 | Header, 4-Pin, Dual row | 1
key | Jumper | Jumper | K0, K1, WKUP | Jumper Wire | 3
PR4 | 4x1K | RR-4x100k-1206PR1, PR2, PR3 | 3
BAT54C | BAT54C | BAT54C | Q1 | | 1
PNP_SOT23 | 9012 | PNP | Q2 | PNP Bipolar Transistor | 1
NPN_SOT23 | 9013 | 2N3904 | Q3, Q4 | NPN General Purpose Amplifier | 2
RC0603 | 1M | Res1 | R1, R20 | Resistor | 2
RC0603 | 22 | RES | R6, R7 | | 2
RC0603 | 1.5K | RES | R8 | | 1
RC0603 | 510R | Res2, RES,
| | RES, RES | R10, R14, R16, R19 | Resistor, [NoValue], [NoValue], [NoValue] | 4
RC0603 | 10K | Res2, Res2,
RES, RES, RES,
| | Res2, Res2,
| | Res2, Res2,
| | Res2, Res2,
| | Res2

R11, R12, R13, R17, R18, R24, R25, R29,

| | | R36, R37, R38, R39 | Resistor, Resistor, [NoValue], [NoValue],
| | | | [NoValue], Resistor, Resistor, Resistor,
| | | | Resistor, Resistor, Resistor, Resistor | 12
RC0603 | 0R | Res2 | R21, R22 | Resistor | 2
RC0805 | 500mA | RES | R40 | | 1
key | Key | Jumper | RST | Jumper Wire | 1
SOT223 | AMS1117-3.3V | 11 | U1 | | 1
TSOP44 | IS62WV51216BL
| L-55TLI

## IS62WV51216BL

| | L-55TLI | U2 | | 1
SOIC8P | W25Q16 | W25X16 | U3 | | 1
LQFP144N | STM32F407ZGT
| 6

## STM32F407ZET

| | 6 | U4 | STM32F407ZET6 | 1
TF_SD | MiniSD | MiniSD | U5 | | 1
SOP16M | CH340G | CH340G | U6 | USB2UART | 1
32.768k | 32.768k | CRYSTAL | Y1 | Crystal 8MHz PLUG | 1
JZ49S | 8MHz | XTAL | Y2 | Crystal Oscillator | 1
JZ49_Com | 12M | CRYSTAL | Y3 | Crystal | 1
| | | | | 97
Approved | | Notes

# mcudev.taobao.com 嵌入式开发网

# 维护您的权益，拒绝使用盗版

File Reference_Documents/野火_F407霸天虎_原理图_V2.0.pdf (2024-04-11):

D

C

B

A | A

目录

# Page 1 目录

# 野火_F407霸天虎_原理图_V2.0

# Page 2

# Page 3

# Page 4

# Page 5

# Page 6

# Page 8

# Page 7

# 历史版本

# 主电源

## MCU_GPIO

## 液晶屏/WIFI

# 引出IO/启动设置

## 串口/RS485/CAN

## 摄像头/SPI闪存/EEPROM

# Page 9 以太网

# Page 10

# Page 11

# 传感器/按键/LED

音频

## Page 12 SRAM/ISP/USB/JTAG/SWD

Title

Size | Document Number | Rev
Date: | Sheet | of
目录 | V2.0

野火_F407霸天虎_原理图

东莞野火电子技术有限公司
https://fire-stm32.taobao.com

A4

Tuesday, March 12, 2019 | 1 | 12

Title

目录 | V2.0

野火_F407霸天虎_原理图

东莞野火电子技术有限公司
https://fire-stm32.taobao.com
Tuesday, March 12, 2019 | 1 | 12

Title

目录 | V2.0

野火_F407霸天虎_原理图

东莞野火电子技术有限公司
https://fire-stm32.taobao.com
Tuesday, March 12, 2019 | 1 | 12

D

C

B

A | A

# 历史版本

# 版本号

V1.0 | 2017-12-1
| 日期 | 设计 | 描述
| | cancore | 初始版本
V2.0 | 2018-12-22 | cancore | 更新结构，增加一个RS232串口，增加一个EBF Module接口

Title

历史版本 | V2.0

野火_F407霸天虎_原理图

东莞野火电子技术有限公司
https://fire-stm32.taobao.com
Tuesday, March 12, 2019 | 2 | 12

Title

历史版本 | V2.0

野火_F407霸天虎_原理图

东莞野火电子技术有限公司
https://fire-stm32.taobao.com
Tuesday, March 12, 2019 | 2 | 12

Title

历史版本 | V2.0

野火_F407霸天虎_原理图

东莞野火电子技术有限公司
https://fire-stm32.taobao.com
Tuesday, March 12, 2019 | 2 | 12

D

# 外部电源供电时断开USB供电，

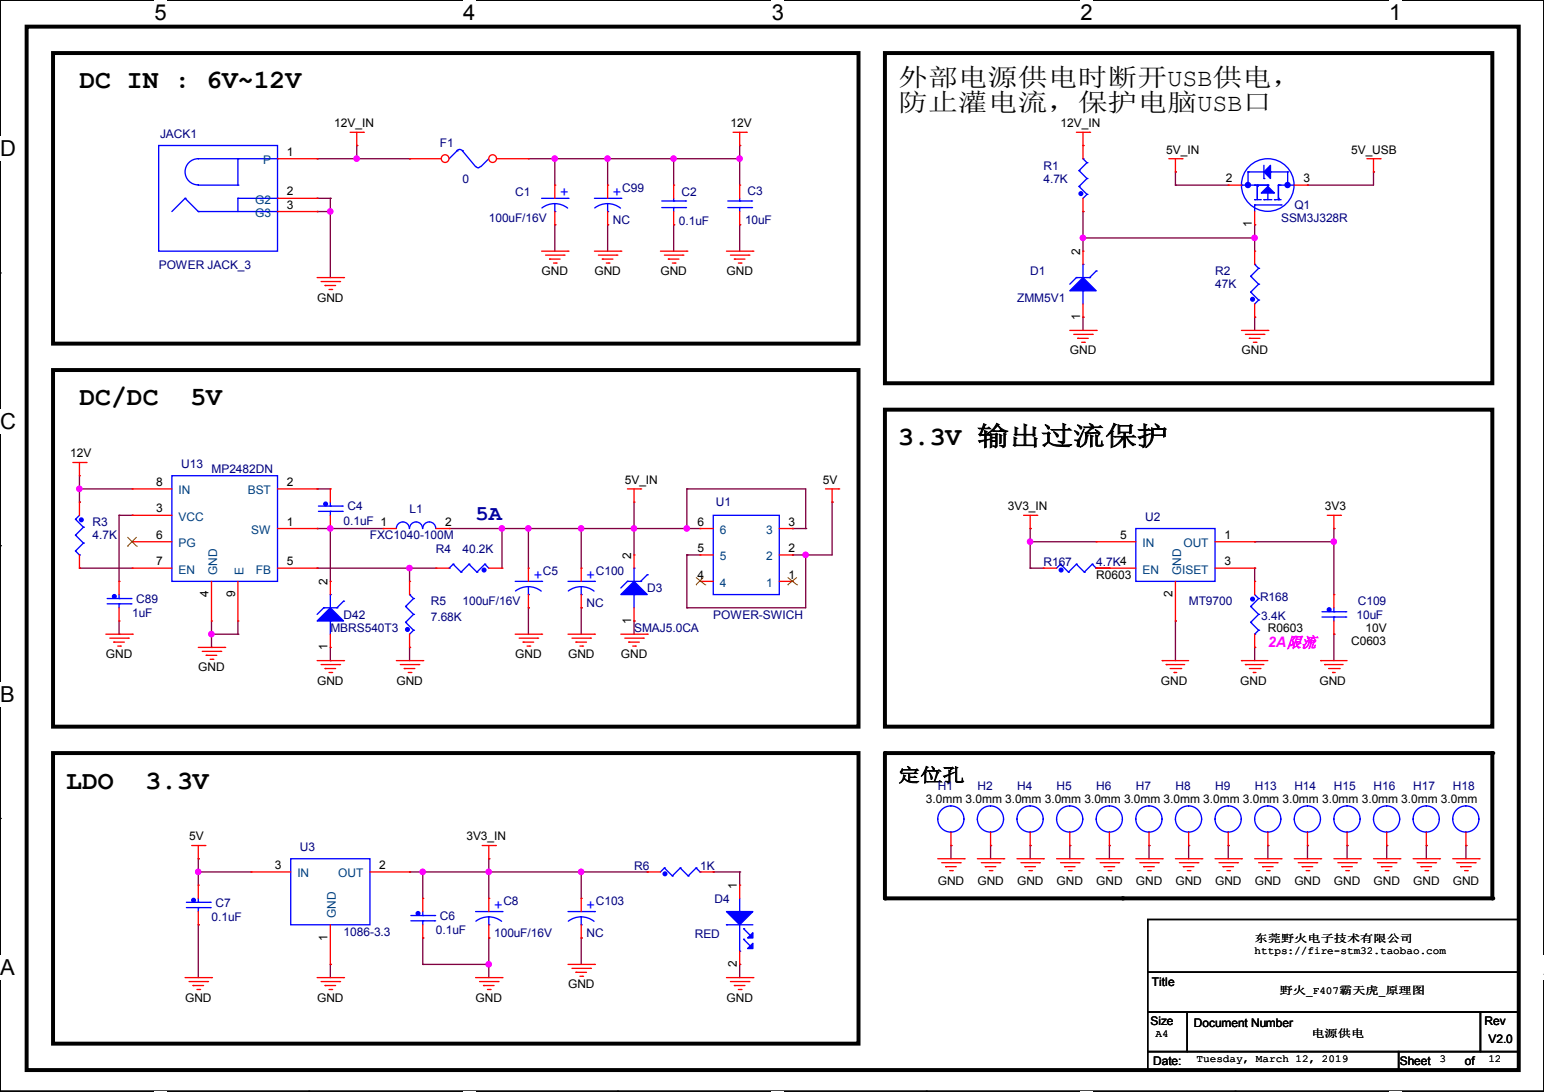
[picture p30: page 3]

GND GND

东莞野火电子技术有限公司
https://fire-stm32.taobao.com

D

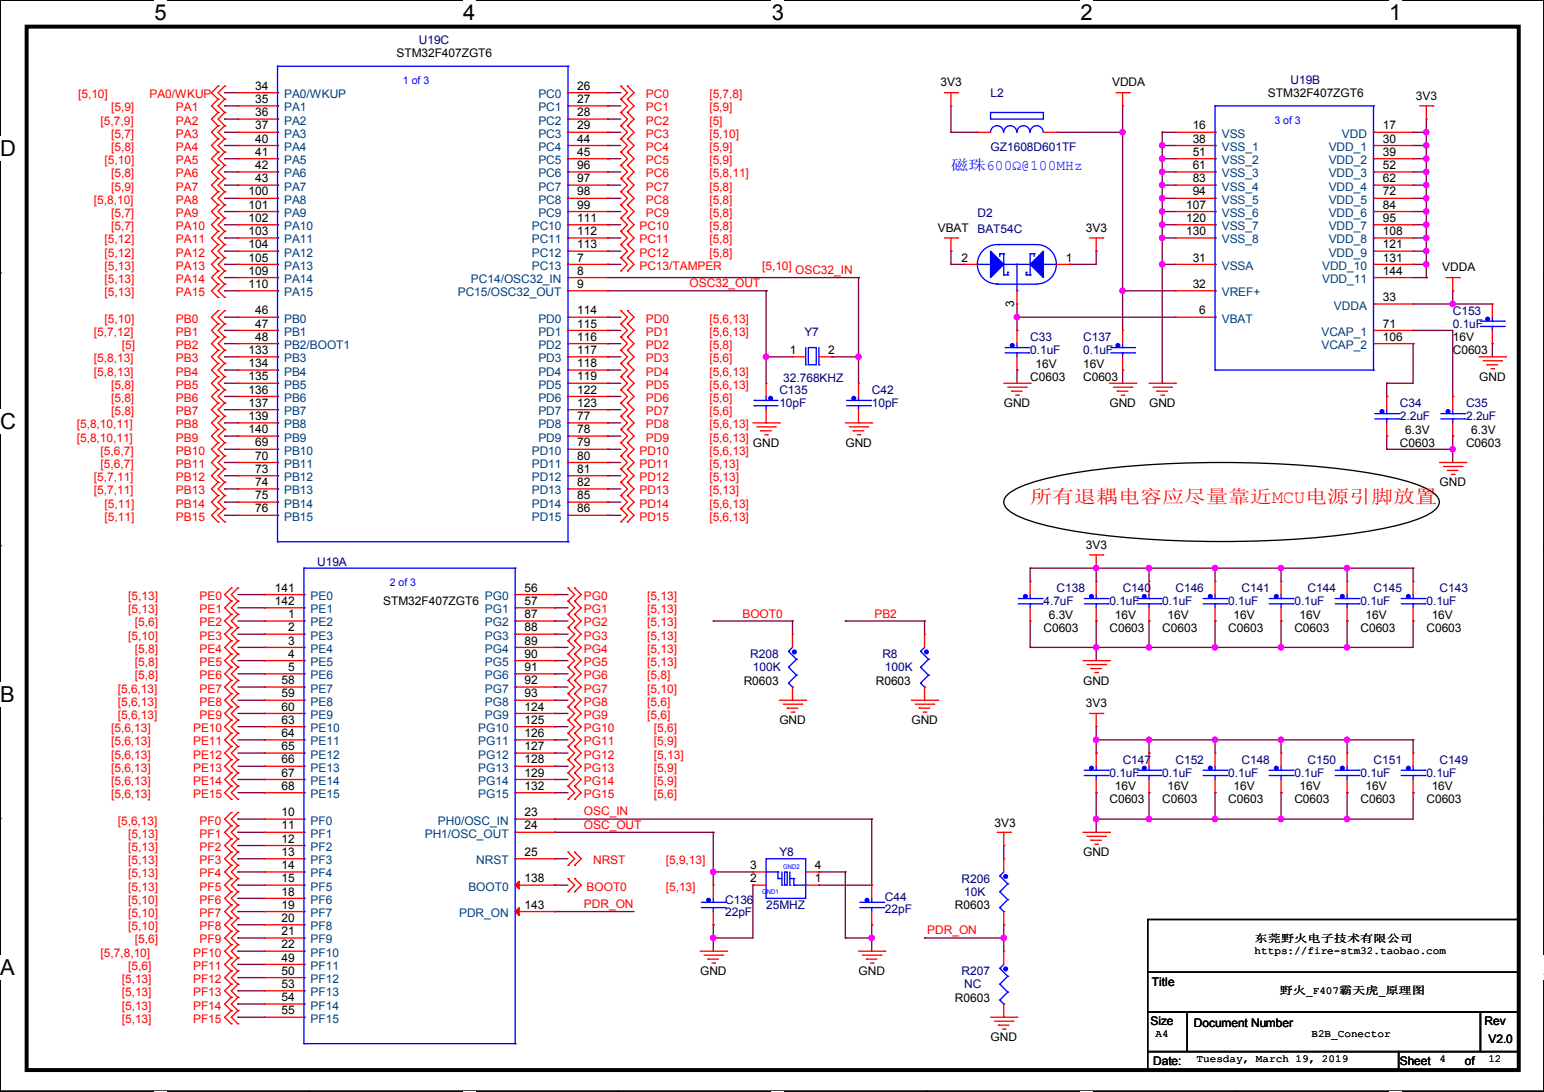
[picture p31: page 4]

东莞野火电子技术有限公司
https://fire-stm32.taobao.com

D

# 引出IO口

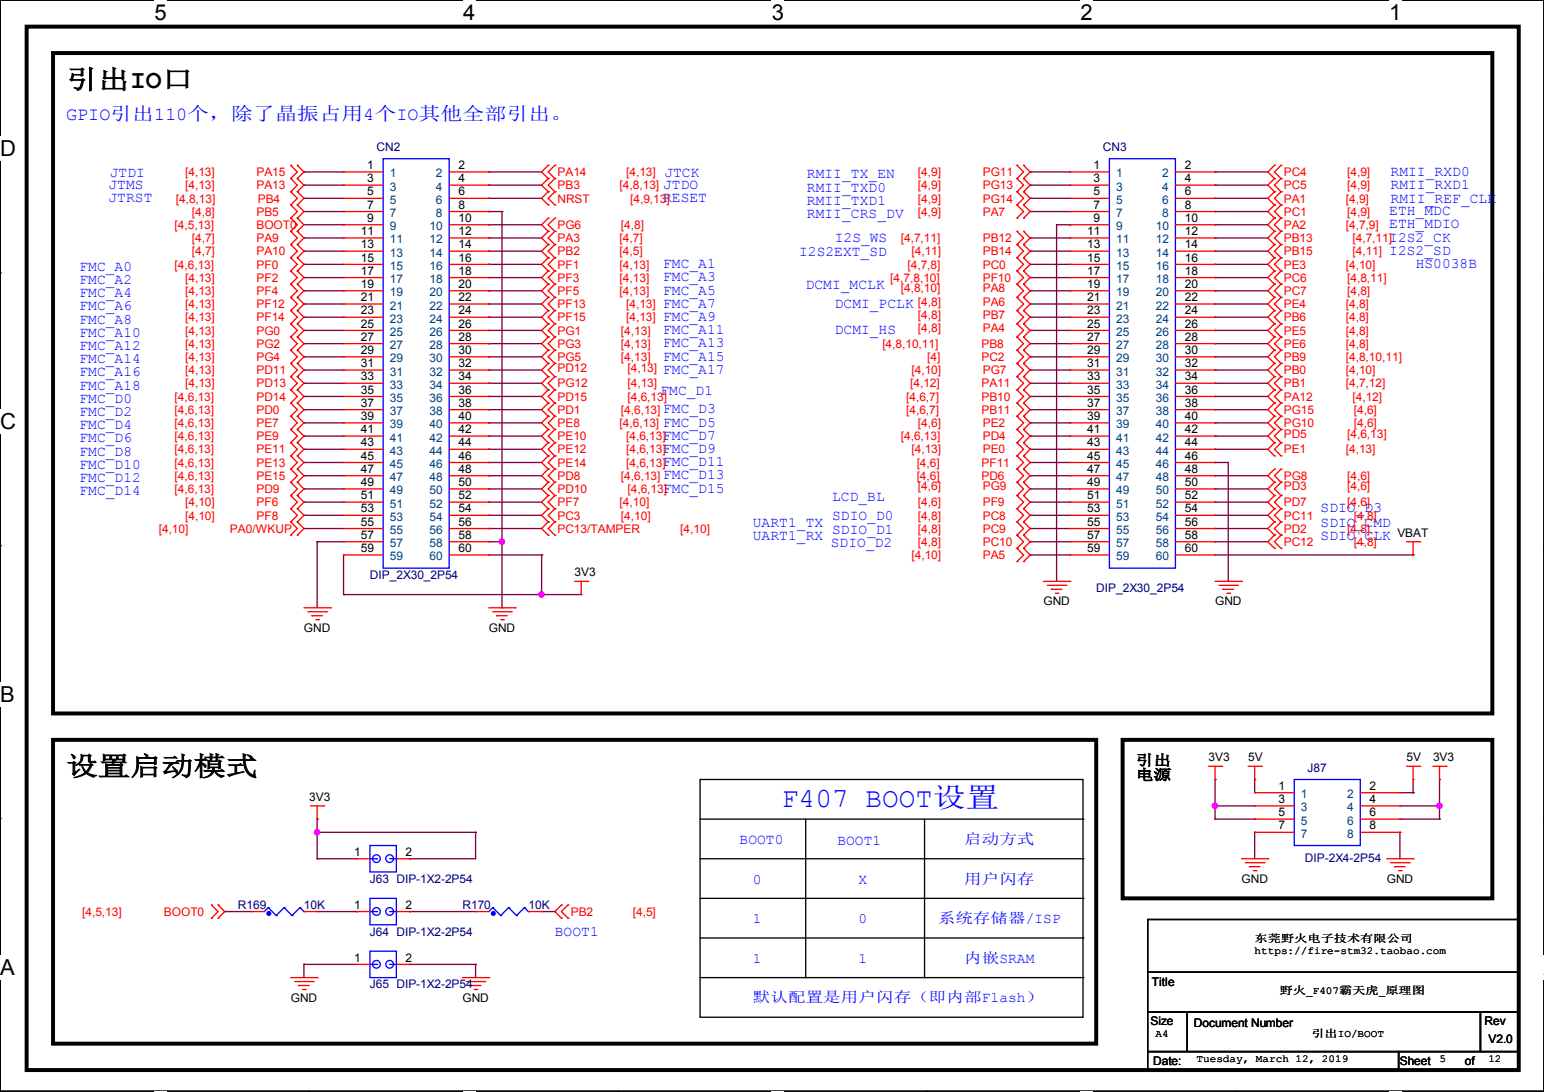
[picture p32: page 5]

东莞野火电子技术有限公司
https://fire-stm32.taobao.com

D

# 液晶接口-FSMC-8080模式

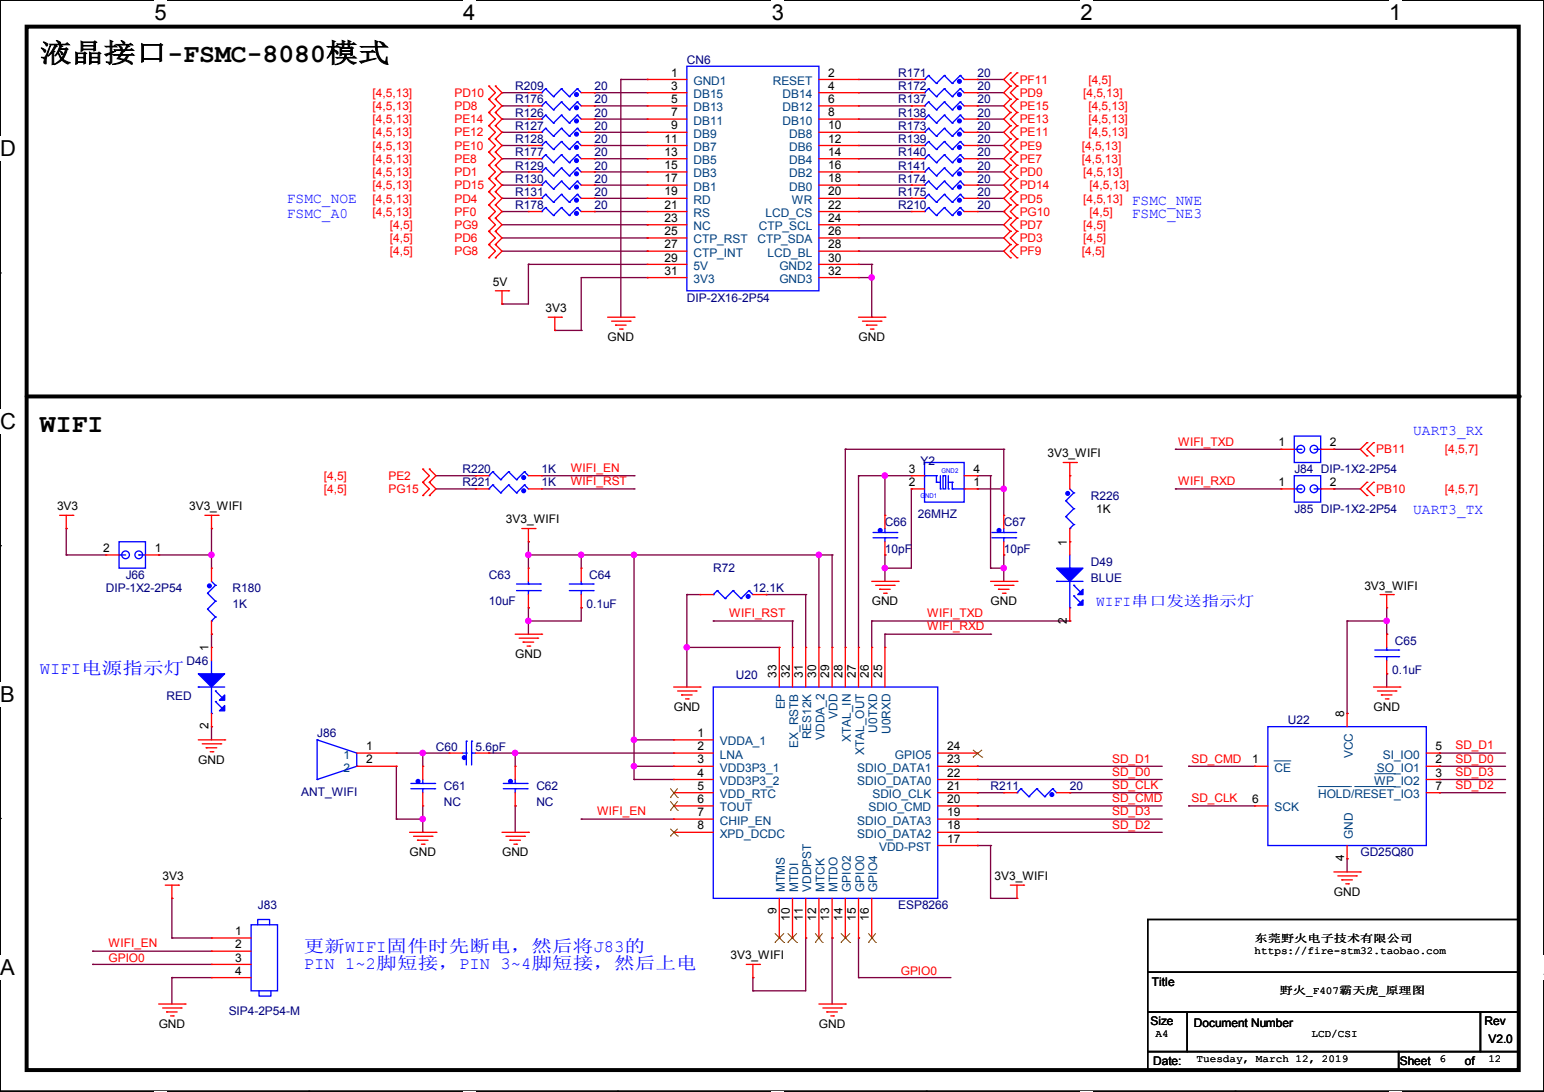
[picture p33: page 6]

东莞野火电子技术有限公司
https://fire-stm32.taobao.com

D

USB转串口 | RS232串口

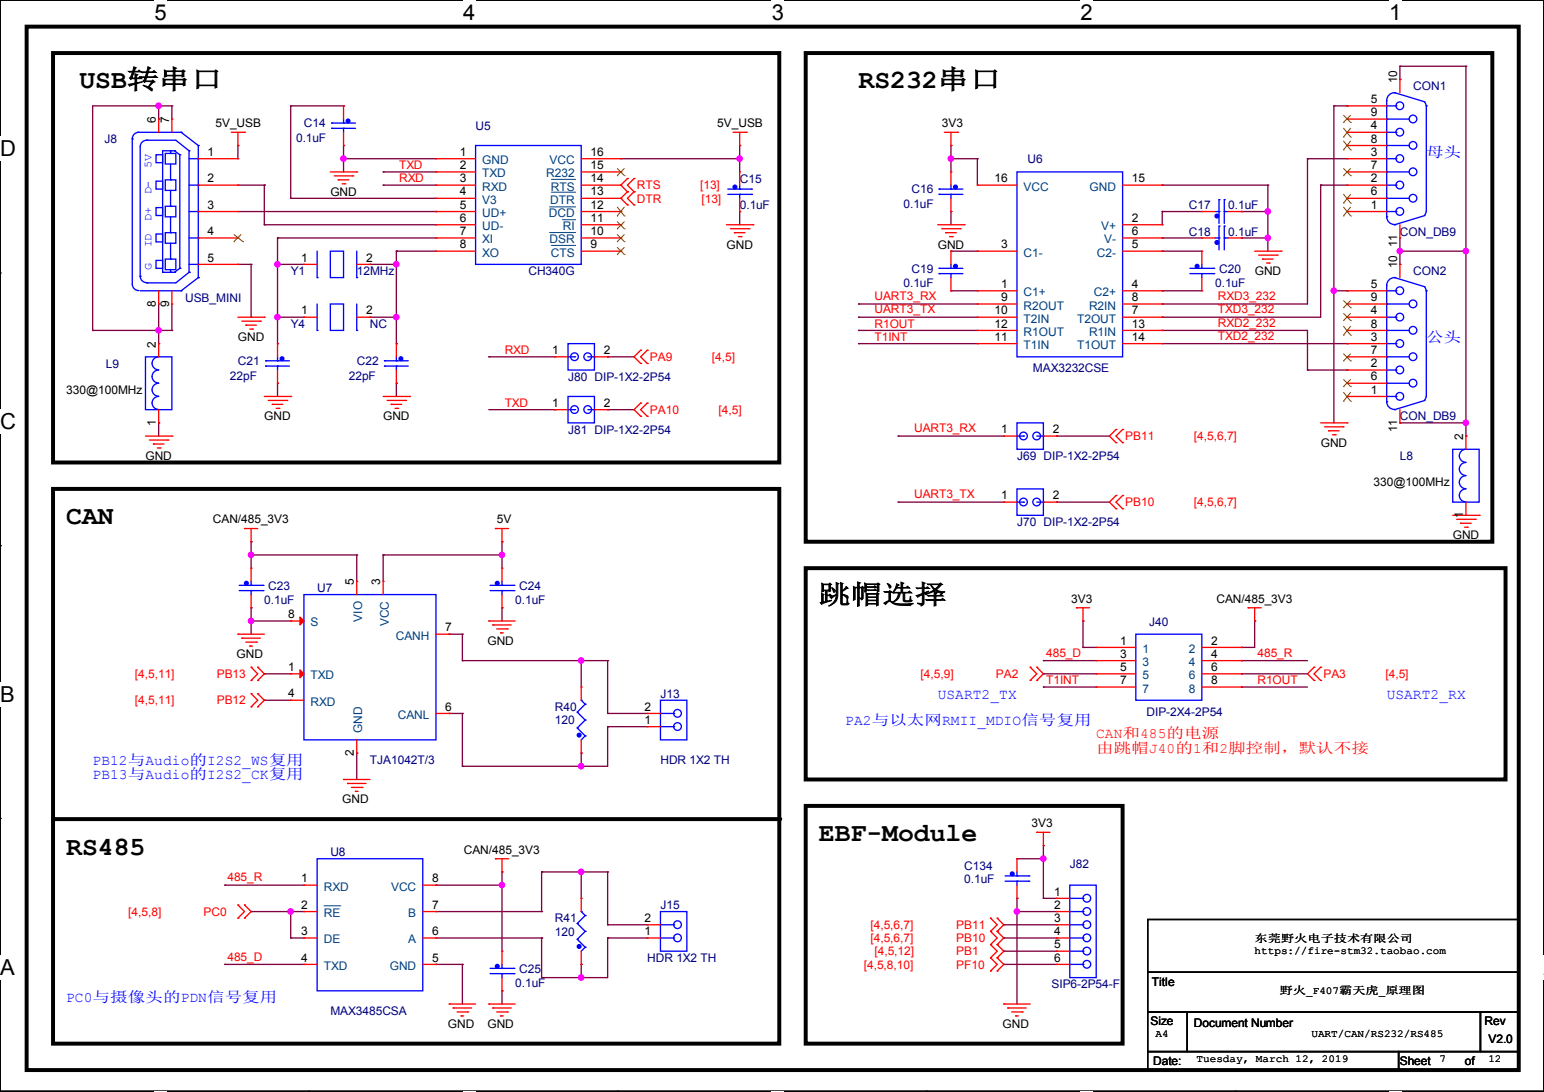
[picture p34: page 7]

东莞野火电子技术有限公司
https://fire-stm32.taobao.com

D

# SD卡

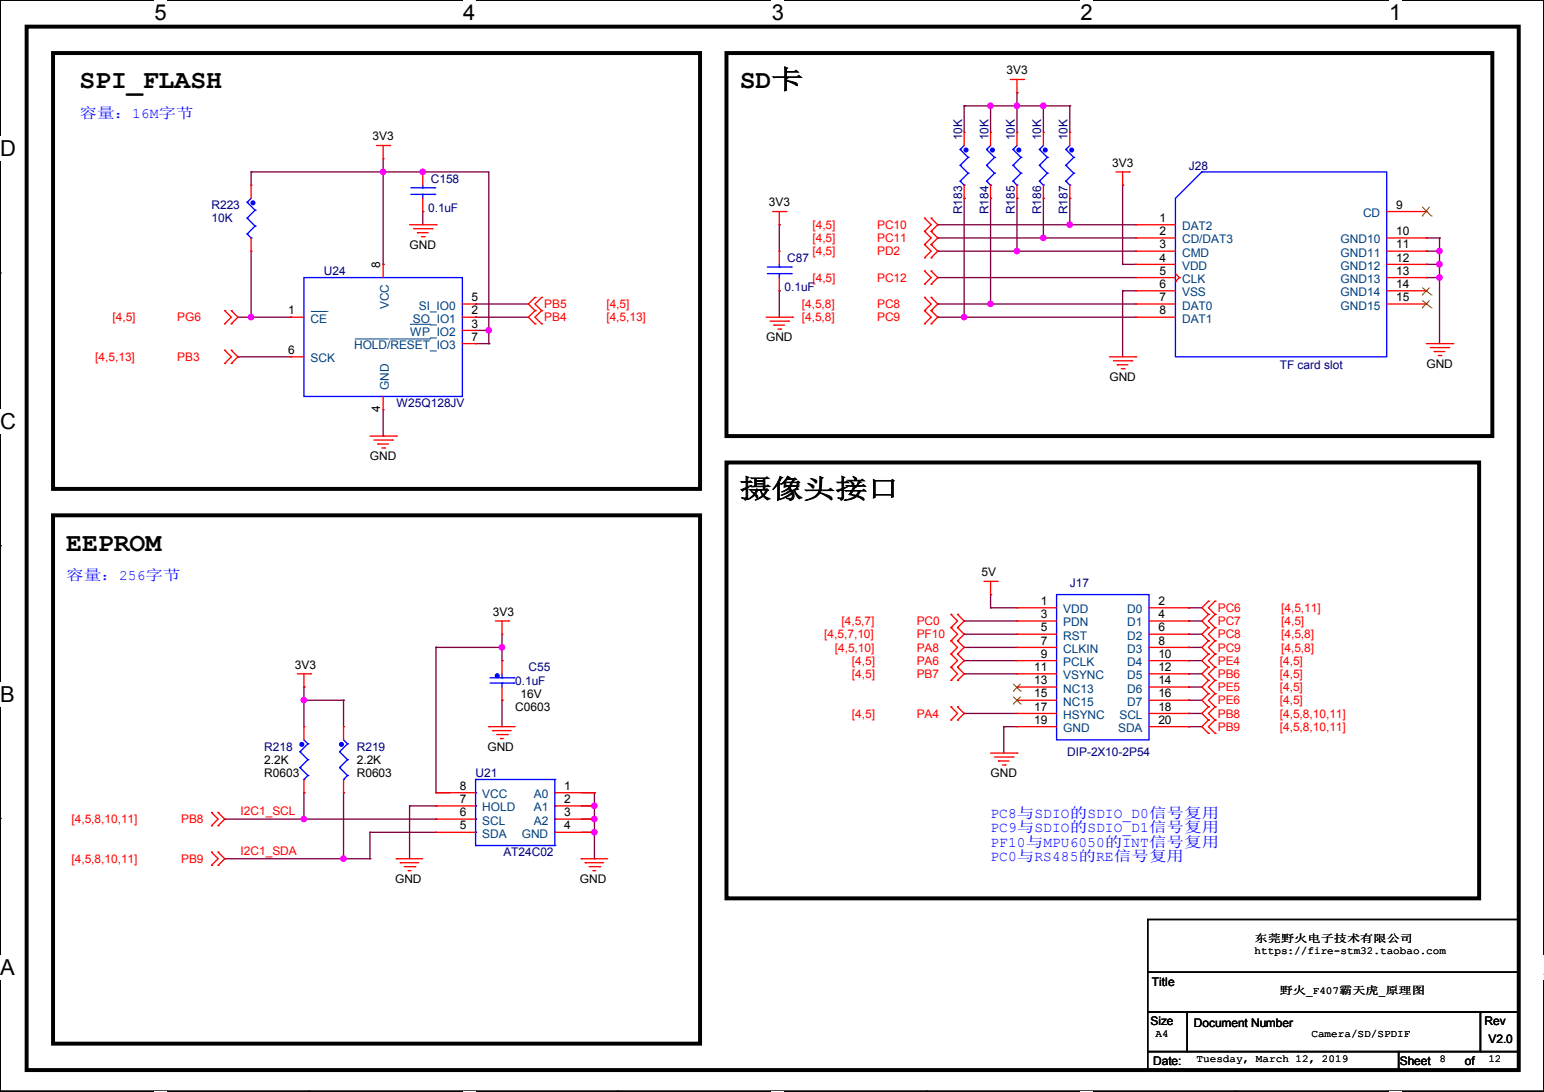
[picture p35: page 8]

东莞野火电子技术有限公司
https://fire-stm32.taobao.com

D

# 以太网接口

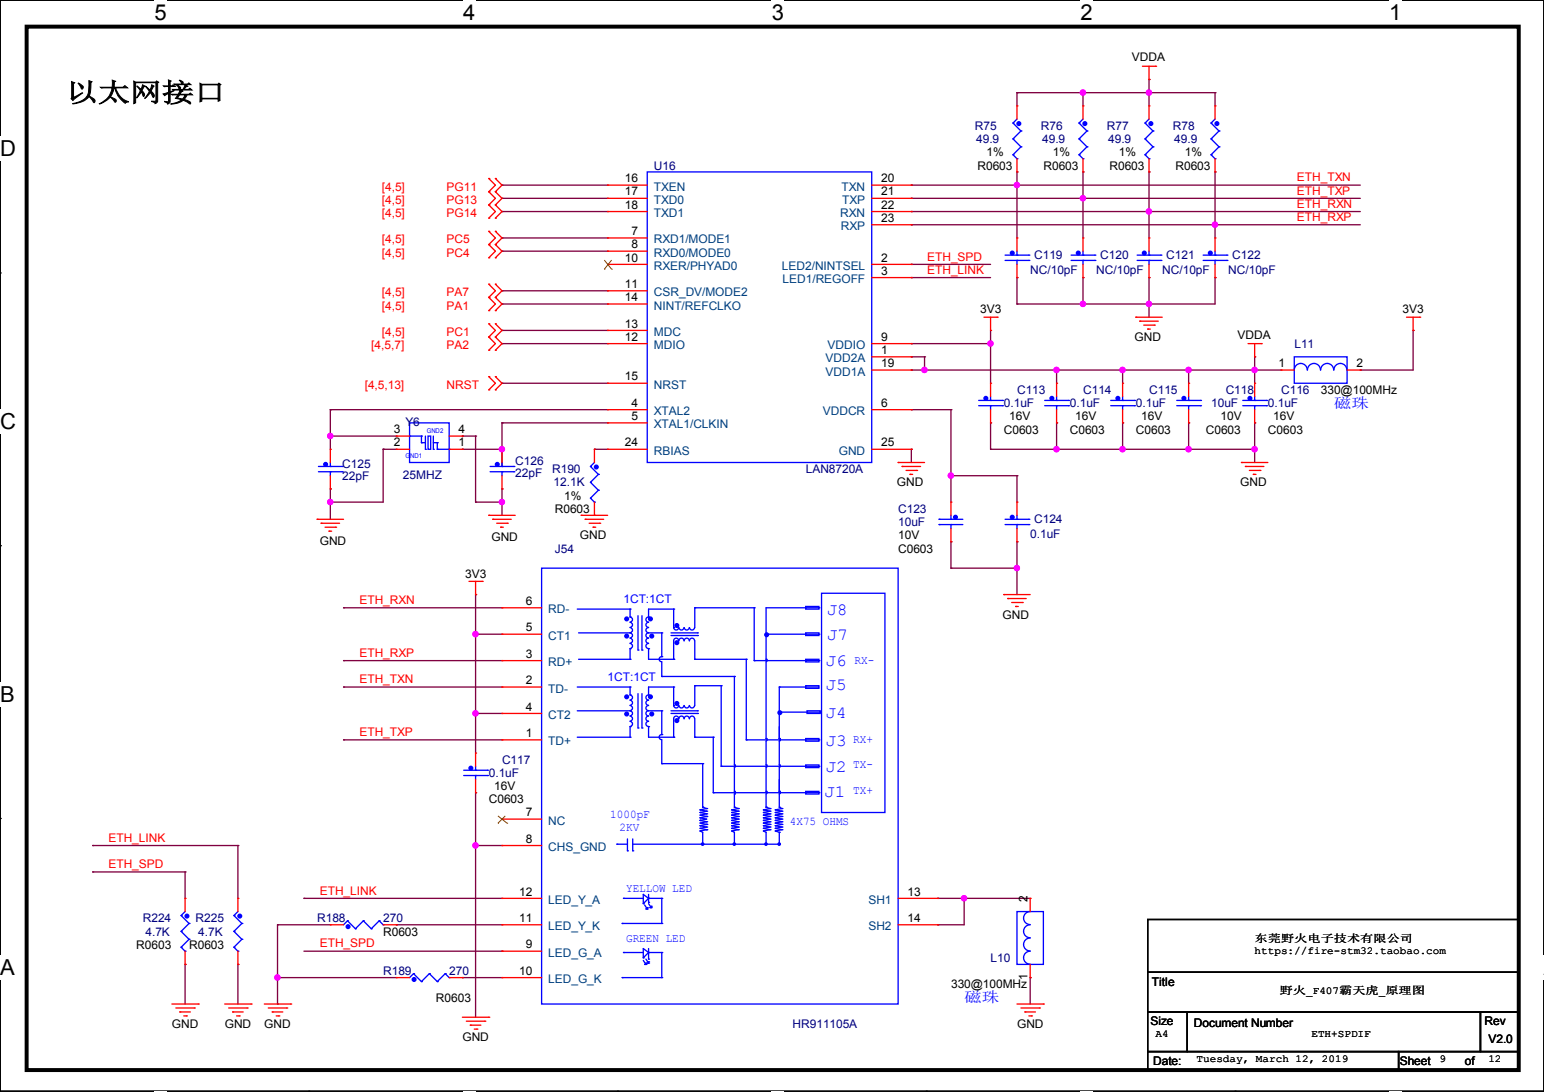
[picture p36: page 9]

东莞野火电子技术有限公司
https://fire-stm32.taobao.com

D

# 六轴传感器

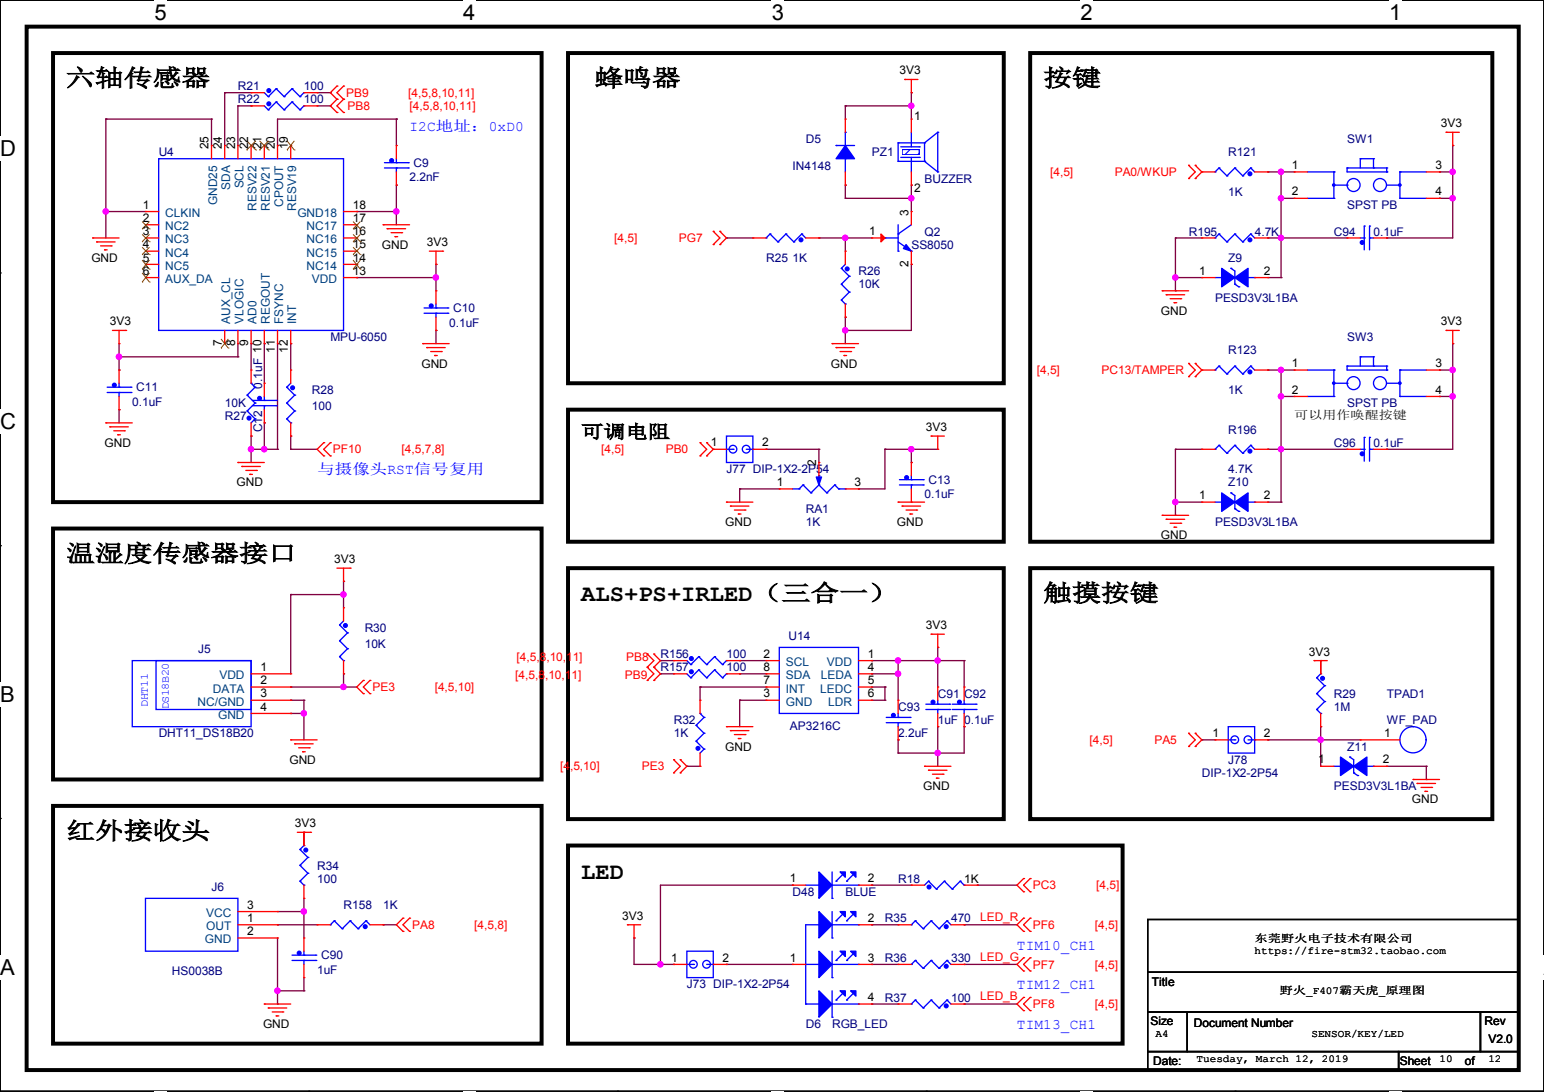
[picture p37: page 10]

ALS+PS+IRLED（三合一）

东莞野火电子技术有限公司
https://fire-stm32.taobao.com

D

# 音频输入

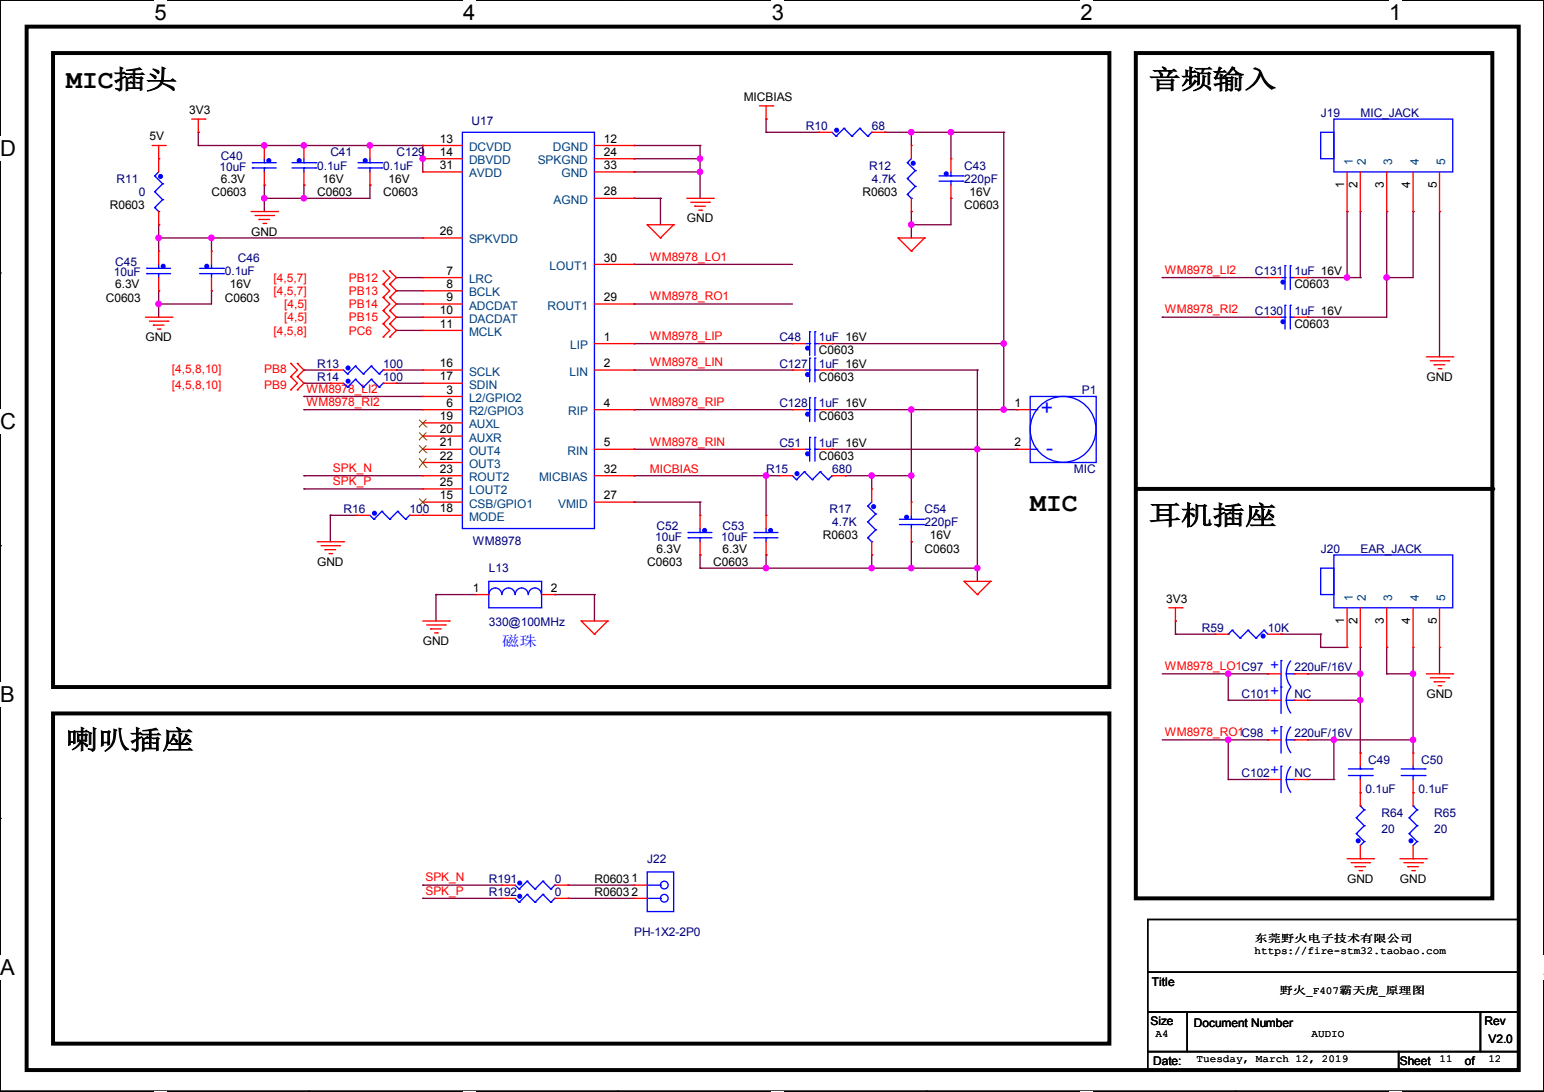
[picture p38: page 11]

东莞野火电子技术有限公司
https://fire-stm32.taobao.com

D

# ISP一键下载电路

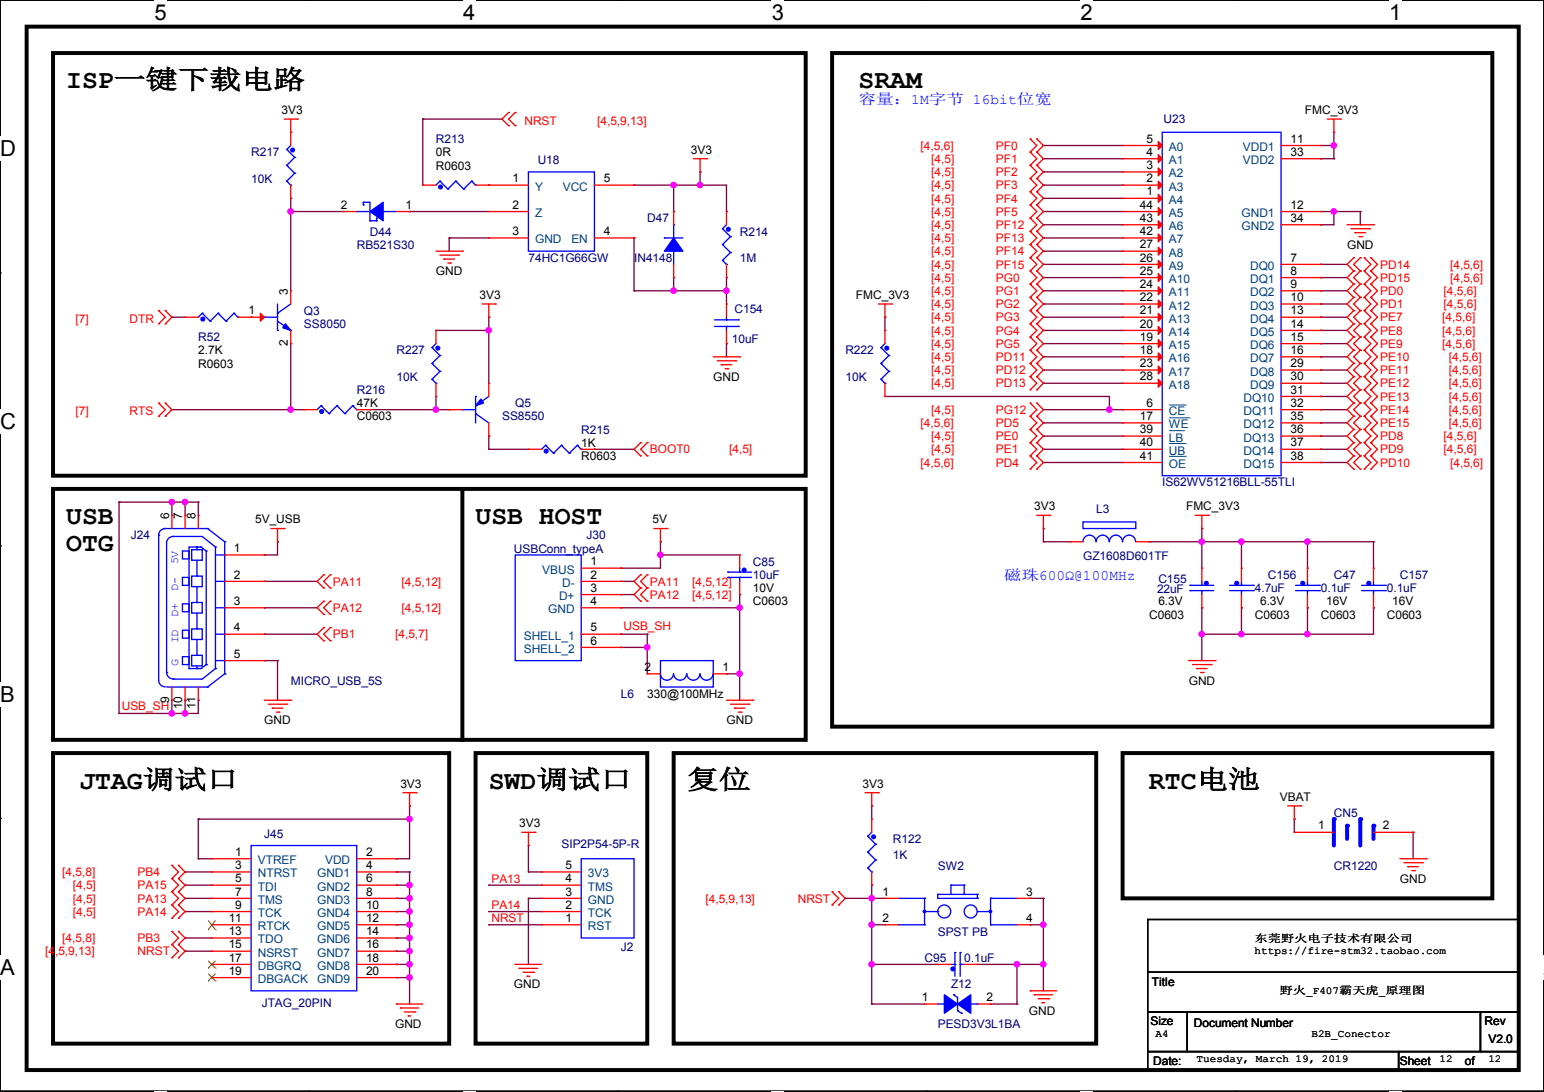
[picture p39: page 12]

东莞野火电子技术有限公司
https://fire-stm32.taobao.com

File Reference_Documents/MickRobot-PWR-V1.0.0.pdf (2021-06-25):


GND

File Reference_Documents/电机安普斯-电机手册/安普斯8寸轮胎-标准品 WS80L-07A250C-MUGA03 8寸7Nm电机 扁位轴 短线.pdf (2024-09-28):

5 3

4 . 5

编码器接线; 3 .2U预绝缘端子; 引线长度; 电机动力接线; 性能要求：; 1、工作电压：36 V DC; 2、最高转速： 2 5 0 R P M ，; 额 定扭矩 7 N m；; 电源电压; 额定转矩（N m）; 额定电流（A）; 瞬间最大转矩（Nm）; 最高转速（ rp m）; 编码器分辨率

3、耐压测试： 6 2 0 V 1 0 m A 1 S
4、无异音、杂音、轮胎摆动等不良。
5、防护等级 I P 6 7。

未注尺寸及形位公差按 : I S O 2 7 6 8 - m K | 设计 | 8寸 7 N m电机 | 型 号

校对 | | 品牌 | 安普斯AMPS

标记 | 分 区 | 更改内容 | 更改文件号 | 签字 | 日期 | | E R P输入

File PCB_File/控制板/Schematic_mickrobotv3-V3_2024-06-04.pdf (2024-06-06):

## 时钟电路

# CAN1


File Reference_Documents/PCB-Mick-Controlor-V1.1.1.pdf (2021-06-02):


2 | 7 | PB4
3 | 6 | PB3

代码地址：https://github.com/RuPingCen/mick_robot_chasiss


1 5

VIN VIN

D 5
SMA J 5.0 A



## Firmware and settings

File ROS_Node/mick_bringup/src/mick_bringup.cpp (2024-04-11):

/**
 * mick四轮差速底盘， 
 * 1、接收cmd_vel 话题的数据，将其转化成转速指令 
 * 2、然后下发到底盘的STM32控制器中
 *  注意：该四轮差速模型与两轮差速模型相同，发送数据的时候需要把1/2号电机的速度设置为一样
 * 3/4号电机速度设置为一样，
  * 
 * 增加IMU数据上传
 * 增加超声波上传
 * 
 * maker:crp
 * 2017-5-13
 */

#include<iostream>
#include<string>
#include <stdlib.h>
#include <stdio.h>
#include <sstream>
#include <vector>
#include <math.h>

#include <ros/ros.h>
#include <ros/spinner.h>
#include <sensor_msgs/CameraInfo.h>
#include <sensor_msgs/Image.h>
#include <std_msgs/String.h>

#include<tf/transform_broadcaster.h>
#include<nav_msgs/Odometry.h>
#include<nav_msgs/Path.h>
#include<geometry_msgs/Twist.h>
#include <sensor_msgs/Joy.h> 
#include <serial/serial.h>
#include <std_msgs/String.h>

#include <boost/asio.hpp>                  //包含boost库函数
#include <boost/bind.hpp>
#include <sys/time.h>

#include <iostream>
#include <fstream>
#include <sstream>
#include <chassis_mick_msg.h>
using namespace std;
using namespace boost::asio;           //定义一个命名空间，用于后面的读写操作

int chassis_type = 0; //默认采用差速模式  0：差速  1-麦克纳姆轮  2: Ackermann  3:4WS4WD
int is_pub_path = 0; //默认不发布小车底盘轨迹  0：不发布   1 发布

float WHEEL_RATIO =19.0; 		//减速比 3508电机减速比为1:19
float WHEEL_K=0.355;            // 麦克纳母轮模式

float WHEEL_L=0.680;                 //左右轮子的间距
float WHEEL_D=0.1525;//0.254; 		    	//轮子直径  10寸的轮子
float WHEEL_R=WHEEL_D/2.0; 			//轮子半径
float WHEEL_PI=3.141693; 			//pi

 
 
nav_msgs::Path path;
serial::Serial ros_ser;
ros::Publisher odom_pub,path_pub;

 
volatile rc_info_t rc;
int rc_init_flags =0;
unsigned int init_times = 0;
int sum_offset[4] = {0};
int show_message =1;
float RC_MIN = 0, RC_MAX = 2500, RC_K = 1; //遥控器摇杆通道输出的最小值、最大值、比例系数
ros::Publisher joy_pub;

moto_measure_t moto_chassis[4] = {0};
moto_measure_t moto_rmd_chassis[4] = {0};
imu_measure_t imu_chassis;  //IMU 数据
//uint16_t Ultrasonic_data [10];   //超声波数据
vector<uint16_t> Ultrasonic_data(10,0);

union floatData //union的作用为实现char数组和float之间的转换
{
    int32_t int32_dat;
    unsigned char byte_data[4];
}motor_upload_counter,total_angle,round_cnt;
union IntData //union的作用为实现char数组和int16数据类型之间的转换
{
    int16_t int16_dat;
    unsigned char byte_data[2];
}speed_rpm,imu;

 
void cmd_vel_callback(const geometry_msgs::Twist::ConstPtr& msg);
void send_speed_to_X4chassis(float x,float y,float w);
void send_rpm_to_chassis( int w1, int w2, int w3, int w4);
void send_speed_to_4WS4WDchassis(float x,float y,float w );
void send_speed_to_Ackerchassis(float x,float w );

void send_rpm_to_4WS4WDchassis(vector<float> vw);

void clear_odometry_chassis(void);
bool analy_uart_recive_data( std_msgs::String serial_data);
void calculate_position_for_odometry(void);
void calculate_chassisAckermann_position_for_odometry(void);
void calculate_chassisAckermann2_position_for_odometry(void);
void publish_odomtery(float  position_x,float position_y,float oriention,float vel_linear_x,float vel_linear_y,float vel_linear_w);
bool publish_joy_msg(void);
int calculate_rc_offset(void);


int main(int argc,char** argv)
{
    string out_result;
    bool uart_recive_flag;
 
//     unsigned char buf[200];                      //定义字符串长度
//     boost::asio::io_service iosev;
//     serial_port sp(iosev, "/dev/ttyUSB0");         //定义传输的串口
//     sp.set_option(serial_port::baud_rate(115200));
//     sp.set_option(serial_port::flow_control());
//     sp.set_option(serial_port::parity());
//     sp.set_option(serial_port::stop_bits());
//     sp.set_option(serial_port::character_size(8));
 
    string sub_cmdvel_topic,pub_odom_topic,dev,joy_topic;
	int baud,time_out,hz;
 	ros::init(argc, argv, "mick robot");
	ros::NodeHandle n("~");
	 
	n.param<std::string>("sub_cmdvel_topic", sub_cmdvel_topic, "/cmd_vel");
	n.param<std::string>("pub_odom_topic", pub_odom_topic, "/odom");
	n.param<std::string>("dev", dev, "/dev/mick");
	n.param<int>("baud", baud, 115200);
	n.param<int>("time_out", time_out, 1000);
	n.param<int>("hz", hz, 100);
	n.param<int>("is_pub_path", is_pub_path, 0); // 默认不发布小车底盘轨迹
	n.param<int>("chassis_type", chassis_type, 3); //  

	n.param<std::string>("joy_topic", joy_topic, "/rc_remotes/joy");
	n.param<float>("RC_K", RC_K, 1);
	n.param<float>("RC_MIN", RC_MIN, 0);
	n.param<float>("RC_MAX", RC_MAX, 2500);

	
	ROS_INFO_STREAM("sub_cmdvel_topic:   "<<sub_cmdvel_topic);
	ROS_INFO_STREAM("pub_odom_topic:   "<<pub_odom_topic);
	ROS_INFO_STREAM("dev:   "<<dev);
	ROS_INFO_STREAM("baud:   "<<baud);
	ROS_INFO_STREAM("time_out:   "<<time_out);
	ROS_INFO_STREAM("hz:   "<<hz);
	ROS_INFO_STREAM("is_pub_path:   "<<chassis_type<<"\t  0:No  1:Yes"); 
	ROS_INFO_STREAM("chassis_type:   "<<chassis_type<<"\t  0:X4  1:M4  2: Ackermann  3:4WS4WD"); 

	ROS_INFO_STREAM("RC_K:   " << RC_K);
	ROS_INFO_STREAM("RC_MIN:   " << RC_MIN);
	ROS_INFO_STREAM("RC_MAX:   " << RC_MAX);
	
	//订阅主题command
	ros::Subscriber command_sub = n.subscribe(sub_cmdvel_topic, 10, cmd_vel_callback);
	//发布主题sensor
	// ros::Publisher sensor_pub = n.advertise<std_msgs::String>("sensor", 1000);
	
	joy_pub = n.advertise<sensor_msgs::Joy>(joy_topic, 20);
	odom_pub= n.advertise<nav_msgs::Odometry>(pub_odom_topic, 20); //定义要发布/odom主题
	path_pub = n.advertise<nav_msgs::Path>(pub_odom_topic+"/path",20, true);
	// 开启串口模块
	 try
	 {
		ros_ser.setPort(dev);
		ros_ser.setBaudrate(baud);
		serial::Timeout to = serial::Timeout::simpleTimeout(1000);
		//serial::Timeout to = serial::Timeout(1,time_out,0,time_out,0);
		to.inter_byte_timeout=1;
		to.read_timeout_constant=5;
		to.read_timeout_multiplier=0;
		ros_ser.setTimeout(to);
		ros_ser.open();
		ros_ser.flushInput(); //清空缓冲区数据
	 }
	 catch (serial::IOException& e)
	 {
		ROS_ERROR_STREAM("Unable to open port ");
		return -1;
	}
	if(ros_ser.isOpen())
	{
		ros_ser.flushInput(); //清空缓冲区数据
		ROS_INFO_STREAM("Serial Port opened");
	}
	else
	{
	    return -1;
	}
 
	ros::Rate loop_rate(hz);

	clear_odometry_chassis();
	bool init_OK=false;
	int init_odom_cnt =0;
	while((!init_OK) && (init_odom_cnt<10))	
	{
		clear_odometry_chassis();
		init_odom_cnt++;
		ROS_INFO_STREAM("clear odometry ..... ");
		if(ros_ser.available())
		{
			std_msgs::String serial_data;
			string str_tem;
			//获取串口数据
			serial_data.data = ros_ser.read(ros_ser.available());
			str_tem =  serial_data.data;
			// cout<<"Recived "<<serial_data.data.c_str()<<endl;
			// ROS_INFO_STREAM(serial_data.data.c_str());
			if(str_tem.find("OK",0) )
			{
				init_OK =true;
				ros_ser.flushInput(); //清空缓冲区数据
			}
		}
		sleep(1);
	}
	ROS_INFO_STREAM("clear odometry successful !");
   
    while(ros::ok())
    { 
		if(ros_ser.available() )
		{
			//ROS_INFO_STREAM("Reading from serial port");
			std_msgs::String serial_data;
			//获取串口数据
			serial_data.data = ros_ser.read(ros_ser.available());
			//cout<<serial_data.data << "\n"<<endl;
			uart_recive_flag = analy_uart_recive_data(serial_data);
			if(uart_recive_flag)
			{
				uart_recive_flag=0;
				if(chassis_type == 0 || chassis_type == 1)
				{
					calculate_position_for_odometry();
				}
				else if(chassis_type == 2)
				{
					 calculate_chassisAckermann_position_for_odometry();
				}
				else
				{
					;
				}
			    // odom_pub.publish(serial_data);//将串口数据发布到主题sensor
			}
			else
			{
				ROS_WARN_STREAM(" analy uart recive data error ...");
				//serial_data.data = ros_ser.read(ros_ser.available());
				ros_ser.flushInput(); //清空缓冲区数据
				sleep(0.2);            //延时0.1秒,确保有数据进入
			}
		}
		ros::spinOnce();
		loop_rate.sleep();	
    }
   
    std::cout<<" EXIT ..."<<std::endl;
    ros::waitForShutdown();
    ros::shutdown();
    return 1;
}
void cmd_vel_callback(const geometry_msgs::Twist::ConstPtr& msg)
{
//ROS_INFO_STREAM("Write to serial port" << msg->data);
 // ostringstream os;
  float speed_x,speed_y,speed_w;
  float v1=0,v2=0,v3=0,v4=0;
  // os<<"speed_x:"<<msg->linear.x<<"      speed_y:"<<msg->linear.y<<"      speed_w:"<<msg->angular.z<<'\n';
 //cout<<os.str()<<endl;
//send_speed_to_chassis(msg->linear.x*10,msg->linear.y*10,msg->angular.z*2);

  
  speed_x = msg->linear.x;
  speed_y = 0;
  speed_w = msg->angular.z;
  

	if(chassis_type == 0) //差速模式
	{
		v1 =speed_x-0.5*WHEEL_L*speed_w;   //左边    //转化为每个轮子的线速度
		v2 =v1;
		v4 =-(speed_x+0.5*WHEEL_L*speed_w);
		v3 =v4;
	}
	else if(chassis_type == 1) // 麦克纳姆轮模式
	{
		v1 =speed_x-speed_y-WHEEL_K*speed_w;       //转化为每个轮子的线速度
		v2 =speed_x+speed_y-WHEEL_K*speed_w;
		v3 =-(speed_x-speed_y+WHEEL_K*speed_w);
		v4 =-(speed_x+speed_y+WHEEL_K*speed_w);
	}
	else if(chassis_type == 2) // 阿卡曼模式
	{
		send_speed_to_Ackerchassis(speed_x, speed_w); //直接发送目标速度 和 角速度
		//ROS_INFO_STREAM("send_speed_to_Ackerchassis: "<<speed_x<<"  "<<speed_w);
		return ;
	}
	else if(chassis_type == 3) // 4WS4WD模式
	{
			send_speed_to_4WS4WDchassis(speed_x,speed_y,speed_w);
			ROS_INFO_STREAM("send_speed_to_4WS4WDchassis: "<<speed_x<<"  "<<speed_y<<"  "<<speed_w);
		 	return ;
			// speed_x =-1;
			// speed_y= 1;
			// float v = sqrt(speed_x*speed_x+speed_y*speed_y);


			// float theta = acosf(speed_x/v)*57.3;
			// if(theta>90) //量化到[-pi pi]  
			// 	theta=180-theta;
			// // if(speed_y<0) //位于3/4象限
			// // {
			// // 	theta = -theta;
			// // }
			// if(speed_x<0)  
			// {
			// 	v = -v;
			// }
			// float RPM = v*70.02556; // 轮子直径是258mm               70.02556=60/(3.1515926*0.258); 

			// if(isnanf(theta))
			// {
			// 	ROS_WARN_STREAM("theta is nan ");
			// 	theta=0;
			// }
			// if(theta>92) 
			// 	theta=92;
			// else  if(theta<-92) 
			// 	theta=-92;
			// else;

			// if(RPM>300) 
			// 	RPM=300;
 

			// vector<float> vw;
			// vw.push_back(theta);	vw.push_back(-RPM);   // theta  °/s
			// vw.push_back(theta);	vw.push_back(-RPM);  // RPM  转 /min
			// vw.push_back(theta);	vw.push_back(RPM); 
			// vw.push_back(theta);	vw.push_back(RPM); 
			// vw.push_back(0);	vw.push_back(0);
			// vw.push_back(0);	vw.push_back(0);
			// send_rpm_to_4WS4WDchassis(vw);
			// ROS_INFO_STREAM("send_rpm_to_4WS4WDchassis   theta  : "<<theta<<" RPM "<<RPM);
			// return ;
	}
	else
	{
		ROS_WARN_STREAM("unknown chassis type ! ");
	}

	v1 =v1/(2.0*WHEEL_R*WHEEL_PI);    //转换为轮子的速度　RPM
	v2 =v2/(2.0*WHEEL_R*WHEEL_PI);
	v3 =v3/(2.0*WHEEL_R*WHEEL_PI);
	v4 =v4/(2.0*WHEEL_R*WHEEL_PI);

	v1 =v1*WHEEL_RATIO*60;    //转每秒转换到RPM
	v2 =v2*WHEEL_RATIO*60;
	v3 =v3*WHEEL_RATIO*60;
	v4 =v4*WHEEL_RATIO*60;

  send_rpm_to_chassis(v1,v2,v3,v4);	 
 //send_rpm_to_chassis(200,200,200,200);	
  ROS_INFO_STREAM("v1: "<<v1<<"      v2: "<<v2<<"      v3: "<<v3<<"      v4: "<<v4);
  ROS_INFO_STREAM("speed_x:"<<msg->linear.x<<"      speed_y:"<<msg->linear.y<<"      speed_w:"<<msg->angular.z);
}

// 差速小车
void send_speed_to_X4chassis(float x,float y,float w)
{
  uint8_t data_tem[50];
  unsigned int speed_0ffset=10; //速度偏移值 10ｍ/s，把速度转换成正数发送
  unsigned char i,counter=0;
  unsigned char  cmd;
  unsigned int check=0;
  cmd =0xF3; //针对MickX4的小车使用F3 字段      针对MickM4的小车使用F2
  data_tem[counter++] =0xAE;
  data_tem[counter++] =0xEA;
  data_tem[counter++] =0x0B;
  data_tem[counter++] =cmd;
  data_tem[counter++] =((x+speed_0ffset)*100)/256; // X
  data_tem[counter++] =((x+speed_0ffset)*100);
  data_tem[counter++] =((y+speed_0ffset)*100)/256; // Y
  data_tem[counter++] =((y+speed_0ffset)*100);
  data_tem[counter++] =((w+speed_0ffset)*100)/256; // X
  data_tem[counter++] =((w+speed_0ffset)*100);
  data_tem[counter++] =0x00;
  data_tem[counter++] =0x00;
  for(i=0;i<counter;i++)
  {
    check+=data_tem[i];
  }
  data_tem[counter++] =0xff;
   data_tem[2] =counter-2;
  data_tem[counter++] =0xEF;
  data_tem[counter++] =0xFE;
  ros_ser.write(data_tem,counter);
}
 
/**
 * @function  发送四个点击的转速到底盘控制器
 * ＠param w1 w2 w3 w4 表示四个电机的转速 单位　RPM
 */
void send_rpm_to_chassis( int w1, int w2, int w3, int w4)
{
  uint8_t data_tem[50];
  unsigned int speed_0ffset=10000; //转速偏移10000转

  unsigned char i,counter=0;
  unsigned char  cmd;
  unsigned int check=0;
 cmd =0xF1;
  data_tem[counter++] =0xAE;
  data_tem[counter++] =0xEA;
  data_tem[counter++] =0x0B;
  data_tem[counter++] =cmd;
 
  data_tem[counter++] =(w1+speed_0ffset)/256; // 
  data_tem[counter++] =(w1+speed_0ffset)%256;
  
  data_tem[counter++] =(w2+speed_0ffset)/256; // 
  data_tem[counter++] =(w2+speed_0ffset)%256;
  
  data_tem[counter++] =(w3+speed_0ffset)/256; // 
  data_tem[counter++] =(w3+speed_0ffset)%256;
  
  data_tem[counter++] =(w4+speed_0ffset)/256; // 
  data_tem[counter++] =(w4+speed_0ffset)%256;
 
  for(i=0;i<counter;i++)
  {
    check+=data_tem[i];
  }
  data_tem[counter++] =0xff;
   data_tem[2] =counter-2;
  data_tem[counter++] =0xEF;
  data_tem[counter++] =0xFE;
 
 ros_ser.write(data_tem,counter);
}

void send_speed_to_Ackerchassis(float x,float w)
{
  uint8_t data_tem[50];
  unsigned int speed_0ffset=10; //速度偏移值 10ｍ/s，把速度转换成正数发送
  unsigned char i,counter=0;
  unsigned char  cmd;
  unsigned int check=0;
  cmd =0xF4;  
  data_tem[counter++] =0xAE;
  data_tem[counter++] =0xEA;
  data_tem[counter++] =0x0B;
  data_tem[counter++] =cmd;
  data_tem[counter++] =((x+speed_0ffset)*100)/256; // X
  data_tem[counter++] =((x+speed_0ffset)*100);
  data_tem[counter++] =0; // Y
  data_tem[counter++] =0;
  data_tem[counter++] =((w+speed_0ffset)*100)/256; //  w
  data_tem[counter++] =((w+speed_0ffset)*100);

  for(i=0;i<counter;i++)
  {
    check+=data_tem[i];
  }
  data_tem[counter++] =0xff;
   data_tem[2] =counter-2;
  data_tem[counter++] =0xEF;
  data_tem[counter++] =0xFE;
  ros_ser.write(data_tem,counter);
}
/**
 * @function  发送X Y 方向的速度 以及旋转角速度
 * ＠param  X Y 单位 m/s    w  单位　rad/s
 */
void send_speed_to_4WS4WDchassis(float x,float y,float w)
{
  uint8_t data_tem[50];
  unsigned int speed_0ffset=10; //速度偏移值 10ｍ/s，把速度转换成正数发送
  unsigned char i,counter=0;
  unsigned char  cmd=0xF2; 
  unsigned int check=0;
  
  data_tem[counter++] =0xAE;
  data_tem[counter++] =0xEA;
  data_tem[counter++] =0x0B;
  data_tem[counter++] =cmd;
  data_tem[counter++] =((x+speed_0ffset)*100)/256; // X
  data_tem[counter++] =((x+speed_0ffset)*100);
  data_tem[counter++] =((y+speed_0ffset)*100)/256; // Y
  data_tem[counter++] =((y+speed_0ffset)*100);
  data_tem[counter++] =((w+speed_0ffset)*100)/256; // W
  data_tem[counter++] =((w+speed_0ffset)*100);
  for(i=0;i<counter;i++)
  {
    check+=data_tem[i];
  }
  data_tem[counter++] =0xff;
   data_tem[2] =counter-2;
  data_tem[counter++] =0xEF;
  data_tem[counter++] =0xFE;
  ros_ser.write(data_tem,counter);
}

/**********************************************************
 * @function  发送6个电机的转速到底盘控制器
 * ＠param vw 表示 (w1 v1 w2 v2 .... w6 v6)
 * 电机的转速 单位　RPM
 * 角度    单位  °度
**********************************************************/
void send_rpm_to_4WS4WDchassis(vector<float> vw)
{
	if(vw.size()<12)
	{	
		ROS_WARN_STREAM("For 4ws4wd chasiss, the length of vm < 12");
		return;
	}

  uint8_t data_tem[50];
  unsigned int speed_0ffset=10000; //转速偏移10000转
   unsigned int theta_0ffset=360; 
  unsigned char i,counter=0;
  unsigned char  cmd;
  unsigned int check=0;
  cmd =0xFA;
  data_tem[counter++] =0xAE;
  data_tem[counter++] =0xEA;
  data_tem[counter++] =0x0B;
  data_tem[counter++] =cmd;
 
	i=0;
	for(int j=0;j<6;j++)
	{
		data_tem[counter++] =((vw[ i]+theta_0ffset)*100)/256;
		data_tem[counter++] =((vw[i++]+theta_0ffset)*100);
		data_tem[counter++] =(vw[ i]+speed_0ffset)/256; // 
		data_tem[counter++] =(vw[ i++]+speed_0ffset);
	}
 
  for(i=0;i<counter;i++)
  {
    check+=data_tem[i];
  }
  data_tem[counter++] =0xff;
   data_tem[2] =counter-2;
  data_tem[counter++] =0xEF;
  data_tem[counter++] =0xFE;
 
 ros_ser.write(data_tem,counter);
}

void clear_odometry_chassis(void)
{
  uint8_t data_tem[50];
  unsigned char i,counter=0;
  unsigned char  cmd,resave=0x00;
  unsigned int check=0;
  cmd =0xE1;
  data_tem[counter++] =0xAE;
  data_tem[counter++] =0xEA;
  data_tem[counter++] =0x0B;
  data_tem[counter++] =cmd;
  
  data_tem[counter++] =0x01; //  清零里程计
  data_tem[counter++] =resave;
  
  data_tem[counter++] =resave; // 
  data_tem[counter++] =resave;
  
  data_tem[counter++] =resave; // 
  data_tem[counter++] =resave;
  
  data_tem[counter++] =resave; // 
  data_tem[counter++] =resave;
  
 
  for(i=0;i<counter;i++)
  {
    check+=data_tem[i];
  }
  data_tem[counter++] =0xff;
  data_tem[2] =counter-2;
  data_tem[counter++] =0xEF;
  data_tem[counter++] =0xFE;
 
 ros_ser.write(data_tem,counter);
  
}
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

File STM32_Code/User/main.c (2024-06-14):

/*
* 串口1 与上位机通讯
* 串口2 DBUS DMA接收遥控器数据
* 串口3 485总线
* 串口4 串口5 备用
* 串口6 用于打印调试信息 printf() 函数
*/
#include "stm32f4xx.h"
#include "bsp_systick.h" 
#include "bsp_gpio.h"
#include "bsp_uart.h" 
#include "bsp_timer.h"
#include "bsp_usart_dma.h" 
#include "bsp_can.h" 
#include "bsp_adc.h" 
#include "key.h" 
#include "led.h" 

#include "DBUS/DBUS.h" 
#include "MOTOR_APSL2DB/MOTOR_APSL2DB.h" 
#include "MOTOR_RMD/MOTOR_RMD.h" 
#include "Battery/Battery.h"
#include "Mick_IO/Mick_IO.h"
#include "MOTOR_Control/MOTOR_Control.h"  
#include "MOTOR_EULER.h" 

#include "inv_mpu.h"
#include "inv_mpu_dmp_motion_driver.h"
#include "mpu6050.h"
#include "IO_IIC.h"
#include "IMU.h"
#include "MickRobot_V3.h"

#include "w25q128.h"

#include "lwip/tcp.h"
#include "netconf.h"
#include "tcp_echoclient.h"
#include "stm32f4x7_phy.h"

extern  __IO uint16_t ADC_ConvertedValue[1]; // AD转换DMA数据存储  用于测量输入电压 若低于24V则报警

extern volatile Battery battery; //电池结构体数据


volatile uint32_t Timer2_Counter1=0;  //检测遥控器 通讯是否超时
volatile uint32_t Timer2_Counter2=0; //检测上位机 通讯是否超时
volatile uint32_t Timer2_Counter3=0; //电池读取
volatile uint32_t Timer2_Counter4=0; //IO上传任务
volatile uint32_t Timer2_Counter5=0; // 
volatile uint32_t Timer6_Counter2=0;  // IMU上传
  

volatile uint8_t UART1_Flag;
volatile uint8_t UART2_DMA_Flag=0x00,UART2_DMA_Flag2=0; //串口2中断标志位

volatile uint8_t UART3_Flag; //串口6中断标志位  接收电池
volatile uint8_t USART3_RX_BUF[RS485_RX_Len];  // 串口6 接收缓存
extern volatile uint8_t RS485_Recv_Data[RS485_RX_Len];//电池接收数据
 
volatile uint8_t flag_can1 = 0 ,flag_can1_2=0;		 //用于标志是否接收到数据，在中断函数中赋值
volatile uint8_t flag_can2 = 0;		  
//volatile CanTxMsg CAN2_TxMessage;		 //发送缓冲区
volatile CanRxMsg CAN1_RxMessage;		  //接收缓冲区
volatile CanRxMsg CAN2_RxMessage;		  //接收缓冲区
//extern uint8_t data_can[8];

extern volatile moto_measure_t moto_chassis[4];

volatile uint8_t motor_errors_cnt=0; //电机报错次数
volatile uint8_t motor_detect_cnt=0; //电机状态监测次数

// 以太网测试变量
extern __IO uint8_t EthLinkStatus;
__IO uint32_t LocalTime = 0;


static void TIM3_Config(uint16_t period,uint16_t prescaler);
void Main_Delay(unsigned int delayvalue);
void Test_Mick_IO(void);
int main(void)
{
	uint8_t motor_i=0;
	uint8_t main_counter = 0,IMU_Init_Flag=0;
	uint8_t W25QXX_ID;
	uint8_t W25QXX_SendData[] = "W25Q128读写测试";
	uint8_t W25QXX_Recv[256];
	
	
	SysTick_Init(); //滴答定时器初始化
	Initial_micros(); //TIM2 TIM3级联
	
	Init_Mick_GPIO();// 初始化LED 隔离型输出端口

 
	//上位机通讯 串口1
	My_Config_USART_Init(USART1,115200,1);
	UART_send_string(USART1,"USART1 Chassiss for MickRobot-V3 .....\n");

	//printf 占用串口6
	My_Config_USART_Init(USART6,256000,1);
	UART_send_string(USART6,"USART6 Chassiss for MickRobot-V3 .....\n");
	
	// FLASH芯片初始化
	W25QXX_Init();
	W25QXX_ID = W25QXX_ReadID();
	printf("ID:%X\r\n",W25QXX_ID);
	
	// MPU 6050初始化
	printf("Start Init MPU6050 ... \n");
    LED1_FLIP;
	while (mpu_dmp_init() && main_counter<10)
	{
		LED1_FLIP;
		printf("MPU6050 ReInit... \r\n");
		Delay_10us(9000);
		main_counter++;
	}
	if(main_counter<10)
	{
		IMU_Init_Flag = 1;
		printf("MPU6050 Start Success   \r\n");
	}
	else
	{
		printf("MPU6050 Init Failed   \r\n");
	}
	
	// 是否进入测试模式
	Test_Mick_IO();
	
    // DBUS 遥控器   占用串口2
	printf("RC_Remote_Init ...\n");	 
	RC_Remote_Init(); 
	printf("RC_Remote_Init Successful !\n");
	
	// CAN初始化
	printf("CAN1 Init ...\n");	
	CAN_Config(CAN1); //行进电机
	printf("CAN1 Init Successful !\n");	
	
	printf("MOTOR_APSL2DB Init ... \n");
	MOTOR_APSL2DB_Init();
	printf("MOTOR_APSL2DB Init Successful !\n");	
 
    Timer_2to7_Init(TIM6,10*1000);// 10ms
	Timer_start(TIM6);
	
    Timer_2to7_Init(TIM7,50*1000);// 50 ms
	Timer_start(TIM7);
 
	printf("mickrobot-V3 Init seccessful...\n");	
	while(1)
	{
		if(UART2_DMA_Flag) //遥控器介入控制命令逻辑  DBUS 7ms 发送一次数据
		{	
			UART2_DMA_Flag2++;
			if(UART2_DMA_Flag2>10)
			{
				LED2_FLIP;
				Flip_Isolated_Output(3);//绿色
				
				if(Send_RC_Message)
				{
					RC_Upload_Message();//上传遥控器状态
				}
				if(Debug_RC_Message)
				{
					RC_Debug_Message();
				}
				UART2_DMA_Flag2=0;
			}			
			UART2_DMA_Flag=0x00;	
		}
		
		if(flag_can1)
		{
			flag_can1_2++;
			if(flag_can1_2>3)
			{
				flag_can1_2 = 0;
				LED3_FLIP;
			}
				
			//printf("\nStdId: 0x%x   FMI: 0x%x \n",RxMessage.StdId,RxMessage.FMI); 
			//MOTOR_APSL2DB_PDO_Debug();
			
			if((moto_chassis[0].driver_status != 0x00) //表示有报警
				|| (moto_chassis[1].driver_status != 0x00) 
				|| (moto_chassis[2].driver_status != 0x00) 
				|| (moto_chassis[3].driver_status != 0x00))
			{
				motor_errors_cnt++; //每隔1秒清除一次计数	
				motor_i=0;
				for(motor_i=0;motor_i<4;motor_i++)
				{
					if((moto_chassis[0].driver_status != 0x00)) //表示有报警
					{
						 printf("Motor ID: %d  with warning !!!\n",motor_i);	
						if(((moto_chassis[motor_i].error_code_LSB & 0x80) || (moto_chassis[motor_i].error_code_HSB & 0x08)) 
							&& motor_errors_cnt<10) //驱动器输出短路 
						{
							    printf("Motor ID: %d  is overhead, now clear the error flag with reset APSL2DB\n",motor_i);	
								MOTOR_APSL2DB_Init();
						}
						else
						{
							Set_Isolated_Output(4,1);//红
						}
					}
				}				
			}
			else
			{
				Set_Isolated_Output(4,0);//红
			}
			if(Send_Motor_Message)
				Chassis_Motor_Upload_Message();
			if(Send_Odom_Message)
				Chassis_Odom_Upload_Message();
			flag_can1=0;
		}
		// IMU 数据读取 上传
		if(IMU_Init_Flag && Timer6_Counter2 > 1) //10ms  100HZ 读取DMP
		{
			IMU_Routing();	
			if(Send_IMU_Message)
			{
				IMU_Upload_Message();	
			}
			Timer6_Counter2=0;
		}
		
		// -----IO 状态上传
		if(Timer2_Counter4>= 20*1) //1秒读取一次 IO状态
		{
			Isolated_IO_Upload_Message();
			Timer2_Counter4=0;
		}
		
		//------电机状态监测
		if(Timer2_Counter5>= 20*1) //1秒读取一次电机状态
		{
			Timer2_Counter5=0;
			
			motor_errors_cnt=0;  //电机报警次数清零
			
			motor_detect_cnt++;
			if(motor_detect_cnt<5)
				APS_L2DB_Read_Temp(motor_detect_cnt);
			else
			{
				motor_detect_cnt =0;
				if((moto_chassis[0].Temp >= 60) //表示有报警
					|| (moto_chassis[1].Temp >= 60) 
					|| (moto_chassis[2].Temp >= 60) 
					|| (moto_chassis[3].Temp >= 60))
				{
					printf("Motor ID 1-4 tempture: %d, %d, %d, %d \n",moto_chassis[0].Temp,moto_chassis[1].Temp,moto_chassis[2].Temp,moto_chassis[3].Temp);	
					Set_Isolated_Output(4,0);//红
				}
			}
		}
	}
}

 //延时函数 6.3ms
void Main_Delay(unsigned int delayvalue)
{
	unsigned int i;
	while(delayvalue-->0)
	{	
		i=5000;
		while(i-->0);
	}
}
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

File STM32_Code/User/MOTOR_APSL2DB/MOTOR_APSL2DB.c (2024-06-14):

#include "stm32f4xx.h"
#include "string.h"
#include "stdlib.h"
#include "bsp_can.h" 

#include "common.h" 
#include "Mick_IO/Mick_IO.h"

#include "MOTOR_APSL2DB/MOTOR_APSL2DB.h" 
 
 
#define MOTOR_CAN CAN1

volatile moto_measure_t moto_chassis[4] = {0};//4 chassis moto
union INT32 tem_int32;
union INT16 tem_int16;

extern CanRxMsg CAN1_RxMessage;				 //接收缓冲区
extern volatile uint8_t flag_can1;	
/**
* @funtion 安普斯 L2DB 驱动器   CAN open数据协议
* @Brief        
* @Param		
* @Retval	None
* @Date     2023/4/28
* @maker    crp
*/

void MOTOR_APSL2DB_Init(void)
{
	uint8_t index_i=0;
	uint16_t delay_MAX = 50; //延时时间
	uint16_t init_times = 0; //初始化次数
	uint16_t init_times_MAX = 5;
	
	// step0  0x86 清除驱动器报警
   for(index_i=1;index_i<5;index_i++)
	{
		MOTOR_APSL2DB_Enable(index_i,0x06);MOTOR_Delay(delay_MAX);
	}
	for(index_i=1;index_i<5;index_i++)
	{
		MOTOR_APSL2DB_Enable(index_i,0x0F);MOTOR_Delay(delay_MAX);
	}
	printf("MOTOR_APSL2DB_Infor_Get...\n");
	MOTOR_APSL2DB_Infor_Get();
	
	//printf("MOTOR_APSL2DB: step1 check can line is OK?\n");
	// step1  检测CAN总线是连接否正常
	//for(index_i=1;index_i<5;index_i++)
	for(index_i=4;index_i>0;index_i--)
	{
		MOTOR_APSL2DB_Set_Model(index_i,3);// 设置1-4号电机为速度模式
		MOTOR_Delay(delay_MAX);
		init_times = 0;
		while(flag_can1==0 && (init_times++ < init_times_MAX))
		{
			flag_can1 = 0;
			if(CAN1_RxMessage.StdId == 0x580+index_i)
			{
				CAN1_RxMessage.StdId =0x00;
				;//清除接收缓存
			}
			else
			{
				printf("Motro APSL2DB: %d is offline, check CAN bus connection\n",index_i);
			}
		}
		if(init_times == init_times_MAX)
		{
			index_i--;
			printf("Motro APSL2DB: %d not responding, motor init failed\n",index_i);
		}
	}
	
	// step2  0x86 清除驱动器报警
    for(index_i=1;index_i<5;index_i++)
	{
		MOTOR_APSL2DB_Enable(index_i,0x86);MOTOR_Delay(delay_MAX);
	}
	
	 // step3  电机上电(使能)
    for(index_i=1;index_i<5;index_i++)
	{  
		MOTOR_APSL2DB_Enable(index_i,0x0F);MOTOR_Delay(delay_MAX);
		init_times = 0;
		while(flag_can1==0 && (init_times++ < init_times_MAX))
		{
			flag_can1 = 0;
			if((CAN1_RxMessage.StdId == 0x580+index_i) && (CAN1_RxMessage.Data[0] == 0x60))
			{
				break;//清除接收缓存
			}
		}
		if(init_times >= init_times_MAX)
		{
			printf("Motro APSL2DB: %d enable failed\n",index_i);
		}
	}
	printf("Motro APSL2DB: Set Motor IS 1-4 Target speed 0");
	// step4    设置电机目标速度为0 
	for(index_i=1;index_i<5;index_i++)
	{
		MOTOR_APSL2DB_Set_RPM(index_i,0);MOTOR_Delay(delay_MAX);
	}
	
	// step5    设置电机限制电流 25A
	printf("Motro APSL2DB: Set Motor IS 1-4 Current Limt 25");
	for(index_i=1;index_i<5;index_i++)
	{
		MOTOR_APSL2DB_Set_CurrentLimt(index_i,28);MOTOR_Delay(delay_MAX);
	}
	
	
	// step6  梯形加速、减速
	printf("Motro APSL2DB: Set Motor IS 1-4 Trapezoidal Acceleration and Deceleration ");
	for(index_i=1;index_i<5;index_i++)
	{
		MOTOR_APSL2DB_Set_Trap_Accel(index_i,5);MOTOR_Delay(delay_MAX);MOTOR_Delay(delay_MAX);
		MOTOR_APSL2DB_Set_Trap_Decel(index_i,13);MOTOR_Delay(delay_MAX);MOTOR_Delay(delay_MAX);
	}
	 
 
	
	// step7    设置电机位置自动上报  PDO 
	for(index_i=1;index_i<5;index_i++)
	{
		MOTOR_APSL2DB_Enable_PDO(index_i,1);MOTOR_Delay(delay_MAX);MOTOR_Delay(delay_MAX);MOTOR_Delay(delay_MAX);
	}

	//APS_L2DB_Read_Position(1);  
}

// 读取电机固件信息 以保证电机是正确连接在CAN总线上
uint8_t MOTOR_APSL2DB_Infor_Get(void)
{
	uint8_t index_i=0,j=0;
	uint16_t delay_MAX = 50; //延时时间
	uint16_t init_times;
	uint16_t init_times_MAX = 50;
	//0x3A 本机型号-系列  默认:L2DB
	//0x30003B 32U,RO ASCII 本机型号-电压与电流等级
	//0x103C 0x30003C   
	//本机型号-反馈与总线类型  默认(485版本):CAFR   默认(CAN版本):CAFC
	//0x103D 0x30003D  本机型号-配方 
						//默认(7Nm电机):ASL3 = 0x41534C33
						//默认(10Nm电机):ASM4 = 0x41536D34
						//默认(15Nm电机):ASM5 = 0x41536D35
						//默认(30Nm电机):ASH8= 0x41534838
	//0x1007 0x2500F1  固件日期 //格式:20190114 代表2019年1月14日
	//0x1009 0x2500F3 32U,RO ASCII 硬件版本
	uint16_t cmd_tem1[] = {0x3000,0x3000,0x3000,0x3000,0x2500,0x2500};
	uint8_t  cmd_tem2[] = {0x3A,0x3B,0x3C,0x3D,0xF1,0xF3};
	for(index_i=1;index_i<5;index_i++)
	{
		for(j=0;j<6;j++)
		{
			
			init_times = 0;
			while(flag_can1==0 )//&& (init_times++ < init_times_MAX))
			{
				LED3_ON;
				MOTOR_APSL2DB_Read_Cmd(index_i,cmd_tem1[j],cmd_tem2[j]); 
				MOTOR_Delay(5000);
				LED3_OFF;
				MOTOR_Delay(5000);
				MOTOR_Delay(5000);
				MOTOR_Delay(5000);
				printf("Motro APSL2DB: %d read motor ID \n",index_i);
			}
			if(init_times >= init_times_MAX)
				printf("Motro APSL2DB: %d read motor ID faild !!!\n",index_i);
			else
				MOTOR_APSL2DB_Measurements_Debug();
		}
	}
	return 0x01;
}

void MOTOR_Delay(uint32_t delayvalue)
{
	unsigned int i;
	while(delayvalue-->0)
	{	
		i=5000;
		while(i-->0);
	}
}
 

// 设置电机工作模式   3 带加减速控制的速度模式 -3 立即速度模式 4 力矩模式 1 位置模式
void MOTOR_APSL2DB_Set_Model(uint16_t ID, int8_t param_value)
{
	uint16_t index = 0x6060;
	uint8_t subindex = 0x00;
    CanTxMsg TxMessage;
	TxMessage.StdId = 0x600+ID;
	TxMessage.IDE = CAN_ID_STD;
	TxMessage.RTR = CAN_RTR_DATA;
	TxMessage.DLC = 0x08;
	TxMessage.Data[0] = 0x2F; //一个字节
	TxMessage.Data[1] = index;
	TxMessage.Data[2] = index >> 8;
	TxMessage.Data[3] = subindex;
	TxMessage.Data[4] = param_value;
	TxMessage.Data[5] = 0x00;
	TxMessage.Data[6] = 0x00;
	TxMessage.Data[7] = 0x00;
	CAN_Transmit(MOTOR_CAN, &TxMessage); // 发送消息  
}
// 设置电机工作模式   0x06 电机断电（松轴） 0x0F 电机上电(使能)  0x86 清除驱动器报警
void MOTOR_APSL2DB_Enable(uint16_t ID, int16_t param_value)
{
	uint16_t index = 0x6040;
	uint8_t subindex = 0x00;
    CanTxMsg TxMessage;
	TxMessage.StdId = 0x600+ID;
	TxMessage.IDE = CAN_ID_STD;
	TxMessage.RTR = CAN_RTR_DATA;
	TxMessage.DLC = 0x08;
	TxMessage.Data[0] = 0x2B;
	TxMessage.Data[1] = index;
	TxMessage.Data[2] = index >> 8;
	TxMessage.Data[3] = subindex;
	TxMessage.Data[4] = param_value;
	TxMessage.Data[5] = 0x00;
	TxMessage.Data[6] = 0x00;
	TxMessage.Data[7] = 0x00;
	CAN_Transmit(MOTOR_CAN, &TxMessage); // 发送消息  
}
// 调用急停以后需要，使用急停解除函数，电机才能控制
// 急停 1:急停生效 0:急停解除
void MOTOR_APSL2DB_EmStop(uint16_t ID, uint8_t param_value)
{
	uint16_t index = 0x605A;
	uint8_t subindex = 0x11;
    CanTxMsg TxMessage;
	TxMessage.StdId = 0x600+ID;
	TxMessage.IDE = CAN_ID_STD;
	TxMessage.RTR = CAN_RTR_DATA;
	TxMessage.DLC = 0x08;
	TxMessage.Data[0] = 0x2F;
	TxMessage.Data[1] = index;
	TxMessage.Data[2] = index >> 8;
	TxMessage.Data[3] = subindex;
	TxMessage.Data[4] = param_value;
	TxMessage.Data[5] = 0x00;
	TxMessage.Data[6] = 0x00;
	TxMessage.Data[7] = 0x00;
	CAN_Transmit(MOTOR_CAN, &TxMessage); // 发送消息  
}

// 设定电机速度 单位RPM
void MOTOR_APSL2DB_Set_RPM(uint16_t ID, double speed_rpm)
{
	uint16_t index = 0x60FF;
	uint8_t subindex = 0x00;
	// 计算速度  ([rpm]*512*[4096])/1875  = rpm*1118.4810666
	int32_t v = (speed_rpm*1118.4810667)/1;
    CanTxMsg TxMessage;
	TxMessage.StdId = 0x600+ID;
	TxMessage.IDE = CAN_ID_STD;
	TxMessage.RTR = CAN_RTR_DATA;
	TxMessage.DLC = 0x08;
	TxMessage.Data[0] = 0x23;
	TxMessage.Data[1] = index;
	TxMessage.Data[2] = index >> 8;
	TxMessage.Data[3] = subindex;
	TxMessage.Data[4] = v;
	TxMessage.Data[5] = v>> 8;
	TxMessage.Data[6] = v>> 16;
	TxMessage.Data[7] = v>> 24;
	CAN_Transmit(MOTOR_CAN, &TxMessage); // 发送消息  
}
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

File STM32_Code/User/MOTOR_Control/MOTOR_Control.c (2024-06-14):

#include "stm32f4xx.h"
#include "math.h"
#include "bsp_uart.h" 
#include "bsp_usart_dma.h" 
#include "bsp_systick.h"
#include "MOTOR_APSL2DB/MOTOR_APSL2DB.h" 
#include "MOTOR_RMD/MOTOR_RMD.h" 
#include "MOTOR_Control/MOTOR_Control.h"  
#include "DBUS/DBUS.h" 
#include "Mick_IO/Mick_IO.h"
#include "IMU.h"


#include "MickRobot_V3.h"


extern imu_Dat IMU_Data;//IMU数据结构体



volatile uint16_t run_cnt=0;

volatile float odom_vx=0,odom_vy=0,odom_w=0;
volatile uint32_t last_time=0,curr_time=0; //用于计算时间 获取积分时间

//将串口1的数据转存到数组 UART1_ReBuff中
volatile uint8_t UART1_ReBuff[100];  
volatile uint16_t UART1_ReCont;  
volatile unsigned char UART1_Reflag; 
command_t recived_cmd;  // 串口1中从上位机解析到的命令

extern rc_info_t rc;  //遥控器
extern volatile uint32_t Timer2_Counter1,Timer2_Counter2;//遥控器和上位机通讯间隔计时

extern volatile moto_measure_t moto_chassis[4];//行进电机状态
extern volatile moto_measure_t moto_rmd_chassis[4];//转向电机状态




/*
 * 包含3种类型底盘控制    差速、阿卡曼、全向


*/

/**
* @funtion	 4轮差速类型底盘
* @Param	 speed_w 范围是 [-1 1]  单位 rad/s
* @Retval	 None
* @Date     2020/8/16
* @maker    crp
*/
void DiffX4_Wheel_Speed_Model(float speed_x,float speed_w)
{
	recived_cmd.speed_available = 0x01;
 
	float v1=0,v2=0,v3=0,v4=0;
	 
	if(speed_x>Chassis_MAX_Speed)
		speed_x =Chassis_MAX_Speed;
	else if(speed_x < -Chassis_MAX_Speed)
		speed_x = -Chassis_MAX_Speed;
	
	speed_w = -speed_w;
	
	if((speed_x>-0.05) && (speed_x<0.05)) 
		speed_x=0;
	
	if((speed_w>-0.05) && (speed_w<0.05)) 
		speed_w=0;

	v1 = speed_x+speed_w*Chassis_Parameter_L;
	v2 = v1; 
	
	v4 = -(speed_x-speed_w*Chassis_Parameter_L);
	v3 = v4;
//	printf("speed_x: %f \tspeed_w %f \n ",speed_x,speed_w);
//	printf("v1-4: %f \t %f\t%f\t%f\t \n ",v1,v2,v3,v4);
	// 使用的是6.5英寸的轮子 直径为17cm  
	recived_cmd.tag_rpm[0] = -(112.344668*v1)/1; // 线速度到RPM的转换系数是   60/(PI*D) = 112.344668
	recived_cmd.tag_rpm[1] = -(112.344668*v2)/1;  // 底盘中心到轮子转动中心的距离是 0.4
	recived_cmd.tag_rpm[2] = -(112.344668*v3)/1;   // speed_w的范围是正负1 是否还需要乘以一个pi 限制旋转速度是pi/s
	recived_cmd.tag_rpm[3] = -(112.344668*v4)/1;
}
// 差速模型底盘 计算里程计
void Calculate_DiffX4_Odom(void)
{
	float vr ,vl;
	float w_tem = 0;
	static float last_yaw =0;
	vr = (moto_chassis[0].speed_rpm + moto_chassis[1].speed_rpm)/2000.0f/112.2336;
	vl = (moto_chassis[3].speed_rpm + moto_chassis[2].speed_rpm)/2000.0f/112.2336;

	odom_vx = (vr+vl)/2.0f;
	odom_vy = 0;
	odom_w = (vr-vl)/0.4f;
	if(IMU_Data.update_flag)
	{
		w_tem = (IMU_Data.yaw-last_yaw)/0.05;
		last_yaw = IMU_Data.yaw;
	}
	// 判断什么情况下使用IMU的角速度
	if(fabs(odom_w) > 0.25)
	{
		if(fabs(w_tem)>0.05)
			odom_w = w_tem;
	}
	else
		odom_w = 0;
}
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

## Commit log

2022-04-23 add SBUS
    [2020型材.SLDPRT, 300.SLDPRT, 320.SLDPRT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]
2022-04-28 modify uart dma init funcation
2023-02-15 增加麦克纳姆轮和差速底盘模式选择
    [M3508附件包_集线板.STEP]
2023-02-16 添加注释
2023-05-28 修复 SBUS初始化失败Bug
2023-11-05 add mpu6050 DMP
    [PCB_Project1.PrjPCB, Sheet3.SchDoc, pcb Rev1.1.2_2021-03-04.pcbdoc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]
2024-01-21 update diffx4 chassis odom calculate model
2024-04-12 update urdf
    [RS-LiDAR-16.stl, RS-LiDAR-32 Interface Box.stl, RS-LiDAR-32.stl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]
2024-06-06 添加轮毂电机连线检测
    [USR-TCP232-Test-V1.3.cfg]
2024-06-14 对输入电压增加AD采样
2024-06-14 添加说明文档
2024-06-14 添加v3控制板说明
2024-09-28 add 3D model
    [M3508附件包_集线板.STEP, Mick小车底盘-清单_20220210.xlsx, USR-TCP232-Test-V1.3.cfg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]
